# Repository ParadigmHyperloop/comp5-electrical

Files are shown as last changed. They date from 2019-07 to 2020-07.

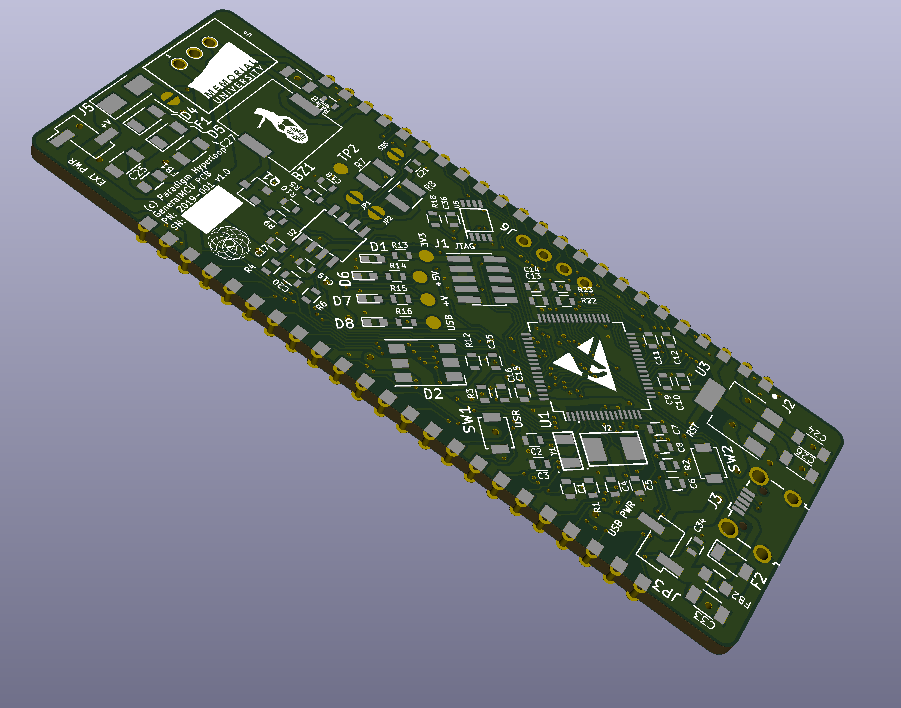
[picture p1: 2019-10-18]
GeneralMCU/pics/Capture2.3.PNG

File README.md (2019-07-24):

# comp5-electrical
All schematics and layouts in KiCad, plus some simulations https://paradigmhyperloop.com

License
See the LICENSE for full licensing details.

In summary, (you still need to read the whole thing), these boards are for Paradigm, and Paradigm only. It is shared with the world for the benefit of observers and potential Paradigm team members. If you wish to utilize these designs in any way, you must contact us first and receive written permission to utilize the designs for the purpose you require.

We don't want to be restrictive, and we will almost certainly grant you permission, but we want to know what you are using our designs for, and we want to make sure you are using them correctly and safely.

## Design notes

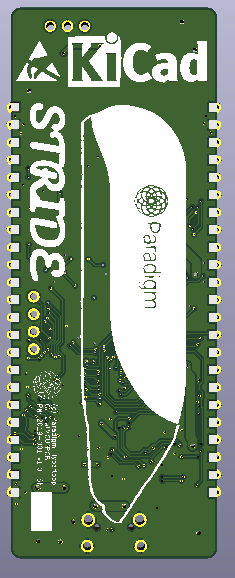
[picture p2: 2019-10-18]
GeneralMCU/pics/Capture2.2.PNG

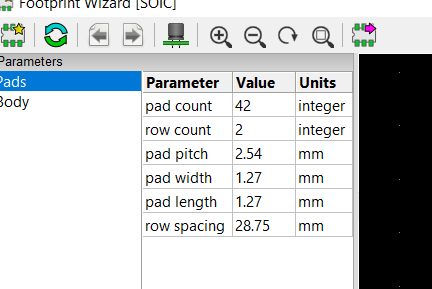
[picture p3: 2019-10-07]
GeneralMCU/pics/Footprint gen settings.PNG

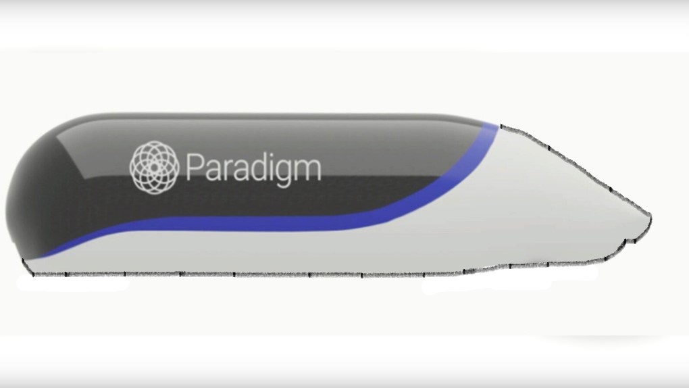
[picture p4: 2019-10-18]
GeneralMCU/pics/poddy.jpg

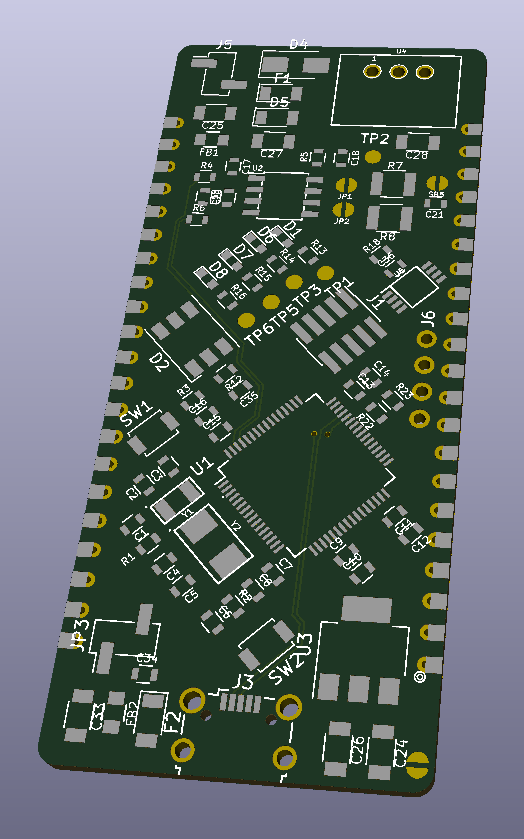
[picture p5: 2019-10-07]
GeneralMCU/docs/Capture1.PNG

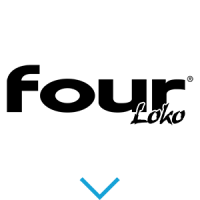
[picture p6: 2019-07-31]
meme_shield_2019/img/FLoko.png

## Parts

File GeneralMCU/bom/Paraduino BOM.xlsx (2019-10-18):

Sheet: BOM V1.0
BOM
Item # | Quantitiy | Value | References | Package | Description | Manufacturer | Manufacturer PN | Supplier | Supplier PN | Unit Cost [$CAD] | Extended [$CAD] | Notes: | Alternates
1 | 1 | Buzzer | BZ1 | Buzzer_Murata_PKMCS0909E4000-R1 | Buzzer, polarized |  |  | Digi-Key | 490-9647-1-ND |  | $0.00
2 | 10 | 0.1u | C1 C6 C7 C9 C11 C13 C15 C18 C19 C36 | SMD_pkg_0603 | Unpolarized capacitor, small symbol |  |  | Digi-Key | 1276-1005-1-ND
3 | 1 | 10n | C8 | SMD_pkg_0603 | Unpolarized capacitor, small symbol |  |  | Digi-Key | 1276-1926-1-ND
4 | 3 | 10u | C25 C27 C33 | SMD_pkg_1206 | Unpolarized capacitor, small symbol |  |  | Digi-Key | 1276-6736-1-ND
5 | 2 | 13p | C2 C3 | SMD_pkg_0603 | Unpolarized capacitor, small symbol |  |  | Digi-Key | 490-1406-1-ND
6 | 7 | 1u | C10 C12 C14 C16 C20 C34 C35 | SMD_pkg_0603 | Unpolarized capacitor, small symbol |  |  | Digi-Key | 1276-1019-1-ND
7 | 2 | 1u | C24 C26 | SMD_pkg_1206 | Unpolarized capacitor, small symbol |  |  | Digi-Key | 1276-1068-1-ND
8 | 1 | 22u | C28 | SMD_pkg_1206 | Unpolarized capacitor, small symbol |  |  | Digi-Key | 1276-6757-1-ND
9 | 1 | 4.7n | C21 | SMD_pkg_0603 | Unpolarized capacitor, small symbol |  |  | Digi-Key | 399-9091-1-ND
10 | 2 | 8p | C4 C5 | SMD_pkg_0603 | Unpolarized capacitor, small symbol |  |  | Digi-Key | 1276-1817-1-ND
11 | 1 | DNP | C17 | SMD_pkg_0603 | Unpolarized capacitor, small symbol |  |  | Digi-Key | ~
13 | 4 | 3V3 +V 5V USB | D1 | LED_0603 | Light emitting diode |  |  | Digi-Key | 732-4966-1-ND
14 | 1 | 40V 1A | D5 | D_1206 | Schottky diode, small symbol, filled shape |  |  | Digi-Key | 478-7805-1-ND
16 | 1 | D_TVS | D4 | D_SMA | Bidirectional transient-voltage-suppression diode |  |  | Digi-Key | SMAJ30ALFCT-ND | *
18 | 1 | WS2812B | D2 | LED_WS2812-PLCC6 | RGB LED with integrated controller |  |  | Digi-Key | 1568-1800-ND
19 | 1 | 32VDC 1A PTC | F1 | D_1206 | Fuse, small symbol |  |  | Digi-Key | 507-1801-1-ND
20 | 1 | 500mA 5V PTC | F2 | D_1206 | Fuse, small symbol |  |  | Digi-Key | 507-1813-1-ND
21 | 2 | FB | FB1 FB2 | SMD_pkg_0805 | Ferrite bead, small symbol |  |  | Digi-Key | 732-1620-1-ND
22 | 1 | ARM_JTAG_SWD | J1 | PinHeader_2x05_P1.27mm_Vertical_SMD | Cortex Debug Connector, standard ARM Cortex-M SWD and JTAG interface |  |  | Digi-Key | 609-6529-ND | http://infocenter.arm.com/help/topic/com.arm.doc.faqs/attached/13634/cortex_debug_connectors.pdf
23 | 1 | OLED | J6 | I2C_OLED | Generic connector, single row, 01x04, script generated (kicad-library-utils/schlib/autogen/connector/) |  |  | Digi-Key | S7002-ND
24 | 1 | USB_B_Micro | J3 | USB_Micro-B_Wuerth-629105150521_CircularHoles | USB Micro Type B connector |  |  | Digi-Key | 609-4616-1-ND
25 | 3 | Jumper_NC_Small | JP1 JP2 JP3 J5 | Pin_Header_Straight_1x02_Pitch2.54mm_SMD_Pin1Left | Jumper, normally closed, small symbol |  |  | Digi-Key | 952-1913-ND
26 | 3 | Jumper_NC_Small | JP1 JP2 JP3 | Pin Jumper |  |  |  | Digi-Key | S9337-ND
27 | 1 | Q_NMOS_DGS | Q1 | SOT-23 | N-MOSFET transistor, gate/source/drain |  |  | Digi-Key | ZXM61N03FCT-ND
28 | 5 | 0 | R4 R6 R11 R20 R21 | SMD_pkg_0603 | Resistor, small US symbol |  |  | Digi-Key | 311-0.0GRCT-ND
29 | 8 | 10k | R1 R2 R3 R12 R13 R14 R15 R16 | SMD_pkg_0603 | Resistor, small US symbol |  |  | Digi-Key | RNCP0603FTD10K0CT-ND
30 | 2 | 1k | R9 R10 | SMD_pkg_0603 | Resistor, small US symbol |  |  | Digi-Key | RNCP0603FTD1K00CT-ND
31 | 3 | 4.7k | R18 R22 R23 | SMD_pkg_0603 | Resistor, small US symbol |  |  | Digi-Key | MCT0603-4.70K-CFCT-ND
32 | 2 | 60 | R7 R8 | SMD_pkg_1210 | Resistor, small US symbol |  |  | Digi-Key | 541-0.0VCT-ND
33 | 1 | DNP | R5 | SMD_pkg_0603 | Resistor, small US symbol |  |  | Digi-Key | ~
34 | 2 | RESET, USER | SW1 SW2 | SW_SPST_B3U-1000P | Push button switch, generic, two pins |  |  | Digi-Key | SW1020CT-ND
36 | 1 | AZ1117-3.3 | U3 | SOT-223-3_TabPin2 | 1A 20V Fixed LDO Linear Regulator, 1.2V, SOT-89/SOT-223/TO-220/TO-252/TO-263 |  |  | Digi-Key | AZ1117EH-3.3TRG1DICT-ND
37 | 1 | DS18B20 | U5 | MSOP-8 | Programmable Resolution 1-Wire Digital Thermometer MSOP-8 |  |  | Digi-Key | DS18B20U+T&RCT-ND | http://datasheets.maximintegrated.com/en/ds/DS18B20.pdf
38 | 1 | P78E05-1000 | U4 | Recom_INNOLINE-R-78E |  |  |  | Digi-Key | 102-5018-ND
39 | 1 | SN65HVD230 | U2 | SOIC-8_N | CAN Bus Transceivers, 3.3V, 1Mbps, Low-Power capabilities, SOIC |  |  | Digi-Key | 296-11654-1-ND | http://www.ti.com/lit/ds/symlink/sn65hvd230.pdf
40 | 1 | STM32F303R6Tx | U1 | LQFP-64_10x10mm_Pitch0.5mm | ARM Cortex-M4 MCU, 32KB flash, 12KB RAM, 72MHz, 2-3.6V, 51 GPIO, LQFP-64 |  |  | Digi-Key | 497-15163-ND | http://www.st.com/st-web-ui/static/active/en/resource/technical/document/datasheet/DM00092070.pdf
41 | 1 | 32.768kHz | Y1 | Crystal_NDK_NX3215SA | Two pin crystal, small symbol |  |  | Digi-Key | 644-1159-1-ND
42 | 1 | 8MHz | Y2 | Crystal_L5_W3.2 | Two pin crystal, small symbol |  |  | Digi-Key | 887-1667-1-ND
43 | 2 |  | J2 | 23 pin tht conn |  |  |  |  | S1012EC-23-ND
 |  |  |  |  |  |  |  |  |  | 1528-2009-ND
 |  |  |  |  |  |  |  | ~ | $49.44

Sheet: Import
Component | Description | Part | References | Value | Footprint | Quantity Per PCB | Datasheet | Datasheet2
1 | Buzzer, polarized | Buzzer | BZ1 | Buzzer | Buzzer_Murata_PKMCS0909E4000-R1 | 1 | 490-9647-1-ND
2 | Unpolarized capacitor, small symbol | C_Small | C1 C6 C7 C9 C11 C13 C15 C18 C19 C36 | 0.1u | SMD_pkg_0603 | 10 | ~
3 | Unpolarized capacitor, small symbol | C_Small | C22 C23 | 0.1u |  | 2 | ~
4 | Unpolarized capacitor, small symbol | C_Small | C8 | 10n | SMD_pkg_0603 | 1 | ~
5 | Unpolarized capacitor, small symbol | C_Small | C25 C27 C33 | 10u | SMD_pkg_1206 | 3 | ~
6 | Unpolarized capacitor, small symbol | C_Small | C2 C3 | 13p | SMD_pkg_0603 | 2 | ~
7 | Unpolarized capacitor, small symbol | C_Small | C10 C12 C14 C16 C20 C34 C35 | 1u | SMD_pkg_0603 | 7 | ~
8 | Unpolarized capacitor, small symbol | C_Small | C24 C26 | 1u | SMD_pkg_1206 | 2 | ~
9 | Unpolarized capacitor, small symbol | C_Small | C28 | 22u | SMD_pkg_1206 | 1 | ~
10 | Unpolarized capacitor, small symbol | C_Small | C21 | 4.7n | SMD_pkg_0603 | 1 | ~
11 | Unpolarized capacitor, small symbol | C_Small | C4 C5 | 8p | SMD_pkg_0603 | 2 | ~
12 | Unpolarized capacitor, small symbol | C_Small | C17 | DNP | SMD_pkg_0603 | 1 | ~
13 | Light emitting diode | LED | D7 | +V | LED_0603 | 1 | ~
14 | Light emitting diode | LED | D1 | 3V3 | LED_0603 | 1 | 732-4966-1-ND
15 | Schottky diode, small symbol, filled shape | D_Schottky_Small_ALT | D5 | 40V 1A | D_1206 | 1 | 478-7805-1-ND
16 | Light emitting diode | LED | D6 | 5V | LED_0603 | 1 | ~
17 | Bidirectional transient-voltage-suppression diode | D_TVS | D4 | D_TVS | D_SMA | 1 | ~
18 | Bidirectional dual transient-voltage-suppression diode, center on pin 3 | D_TVS_x2_AAC | D3 | NUP2105L |  | 1 | ~
19 | Light emitting diode | LED | D8 | USB | LED_0603 | 1 | ~
20 | RGB LED with integrated controller | WS2812 | D2 | WS2812B | LED_WS2812-PLCC6 | 1 | 1568-1800-ND
21 | Fuse, small symbol | Fuse_Small | F1 | 32VDC 1A PTC | D_1206 | 1 | ~
22 | Fuse, small symbol | Fuse_Small | F2 | 500mA PTC | D_1206 | 1 | ~
23 | Ferrite bead, small symbol | Ferrite_Bead_Small | FB1 FB2 | FB | SMD_pkg_0805 | 2 | 732-1620-1-ND
24 | Cortex Debug Connector, standard ARM Cortex-M SWD and JTAG interface | Conn_ARM_JTAG_SWD_10 | J1 | ARM_JTAG_SWD | PinHeader_2x05_P1.27mm_Vertical_SMD | 1 | http://infocenter.arm.com/help/topic/com.arm.doc.faqs/attached/13634/cortex_debug_connectors.pdf
25 | Generic connector, single row, 01x04, script generated (kicad-library-utils/schlib/autogen/connector/) | Conn_01x04 | J4 | Conn_01x04 |  | 1 | ~
26 | Generic connector, single row, 01x04, script generated (kicad-library-utils/schlib/autogen/connector/) | Conn_01x04 | J6 | OLED | I2C_OLED | 1 | ~
27 | Generic connector, single row, 01x02, script generated (kicad-library-utils/schlib/autogen/connector/) | Conn_01x02 | J5 | PWR | Pin_Header_Straight_1x02_Pitch2.54mm_SMD_Pin1Left | 1 | ~
28 | Generic connector, double row, 02x21, counter clockwise pin numbering scheme (similar to DIP packge numbering), script generated (kicad-library-utils/schlib/autogen/connector/) | Conn_02x21_Counter_Clockwise | J2 | SMD castellation PKG |  | 1 | ~
29 | USB Micro Type B connector | USB_B_Micro | J3 | USB_B_Micro | USB_Micro-B_Wuerth-629105150521_CircularHoles | 1 | ~
30 | Jumper, normally closed, small symbol | Jumper_NC_Small | JP1 JP2 SB5 SB6 | Jumper_NC_Small | JUMPER_EGG | 4 | ~
31 | Jumper, normally closed, small symbol | Jumper_NC_Small | JP3 | Jumper_NC_Small | Pin_Header_Straight_1x02_Pitch2.54mm_SMD_Pin1Left | 1 | ~
32 | N-MOSFET transistor, gate/source/drain | Q_NMOS_GSD | Q1 | Q_NMOS_DGS | SOT-23 | 1 | ~
33 | Resistor, small US symbol | R_Small_US | R4 R6 R11 R20 R21 | 0 | SMD_pkg_0603 | 5 | ~
34 | Resistor, small US symbol | R_Small_US | R1 R2 R3 R12 R13 R14 R15 R16 | 10k | SMD_pkg_0603 | 8 | ~
35 | Resistor, small US symbol | R_Small_US | R9 R10 | 1k | SMD_pkg_0603 | 2 | ~
36 | Resistor, small US symbol | R_Small_US | R18 R22 R23 | 4.7k | SMD_pkg_0603 | 3 | ~
37 | Resistor, small US symbol | R_Small_US | R7 R8 | 60 | SMD_pkg_1210 | 2 | ~
38 | Resistor, small US symbol | R_Small_US | R5 | DNP | SMD_pkg_0603 | 1 | ~
39 | Jumper, normally closed, small symbol | Jumper_NC_Small | SB1 SB2 SB3 SB4 | Jumper_NC_Small |  | 4 | ~
40 | Push button switch, generic, two pins | SW_Push | SW2 | RESET | SW_SPST_B3U-1000P | 1 | SW1020CT-ND
41 | Push button switch, generic, two pins | SW_Push | SW1 | USER | SW_SPST_B3U-1000P | 1 | SW1020CT-ND
42 | 1A 20V Fixed LDO Linear Regulator, 1.2V, SOT-89/SOT-223/TO-220/TO-252/TO-263 | AZ1117-3.3 | U3 | AZ1117-3.3 | SOT-223-3_TabPin2 | 1 | AZ1117EH-3.3TRG1DICT-ND
43 | Programmable Resolution 1-Wire Digital Thermometer MSOP-8 | DS18B20U | U5 | DS18B20 | MSOP-8 | 1 | http://datasheets.maximintegrated.com/en/ds/DS18B20.pdf
44 |  | V_REG | U4 | P78E05-1000 | Recom_INNOLINE-R-78E | 1 | 102-5018-ND
45 | CAN Bus Transceivers, 3.3V, 1Mbps, Low-Power capabilities, SOIC | SN65HVD230 | U2 | SN65HVD230 | SOIC-8_N | 1 | http://www.ti.com/lit/ds/symlink/sn65hvd230.pdf
46 | ARM Cortex-M4 MCU, 32KB flash, 12KB RAM, 72MHz, 2-3.6V, 51 GPIO, LQFP-64 | STM32F303R6Tx | U1 | STM32F303R6Tx | LQFP-64_10x10mm_Pitch0.5mm | 1 | 497-15163-ND | http://www.st.com/st-web-ui/static/active/en/resource/technical/document/datasheet/DM00092070.pdf
47 | Two pin crystal, small symbol | Crystal_Small | Y1 | 32.768kHz | Crystal_NDK_NX3215SA | 1 | 644-1159-1-ND
48 | Two pin crystal, small symbol | Crystal_Small | Y2 | 8MHz | Crystal_L5_W3.2 | 1 | 887-1667-1-ND
Component Groups: | 48
Component Count: | 91
Fitted Components: | 91
Number of PCBs: | 1
Total components: | 91
Schematic Version: | v1.0
Schematic Date: | 2019-08-13
BoM Date: | 2019-09-16 18:52
Schematic Source: | C:\projects\hyperloop\comp5-electrical\GeneralMCU\GeneralMCU.sch
KiCad Version: | Eeschema (5.0.2)-1

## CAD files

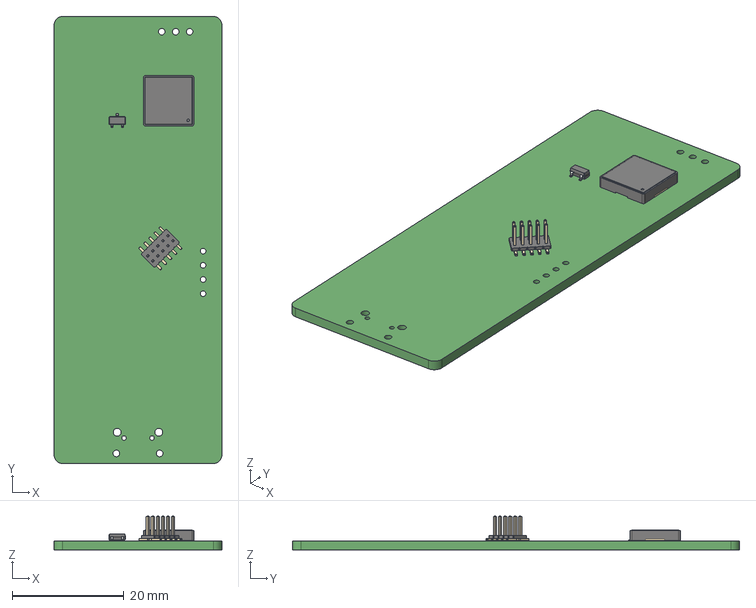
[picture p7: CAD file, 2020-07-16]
BigSur/Models/GeneralMCU.step
30.0 x 80.0 x 6.05 mm

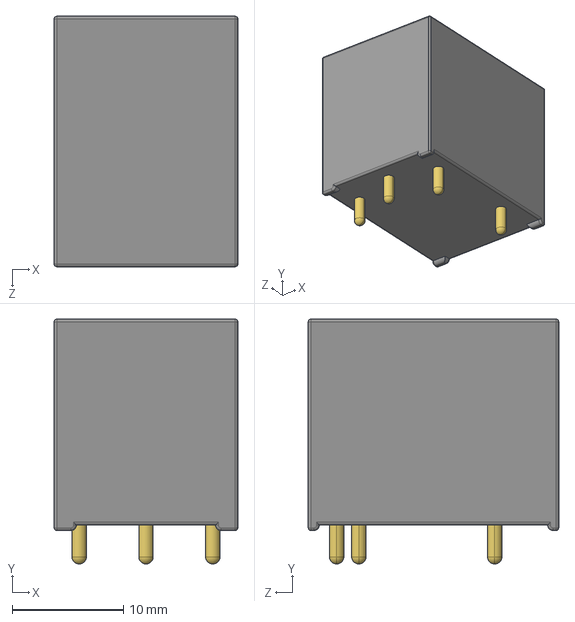
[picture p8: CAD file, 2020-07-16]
BigSur/Models/G5LE-1A-VDDC12.STEP
16.5 x 22.0 x 22.5 mm
Relay_Body
Relay_Contacts

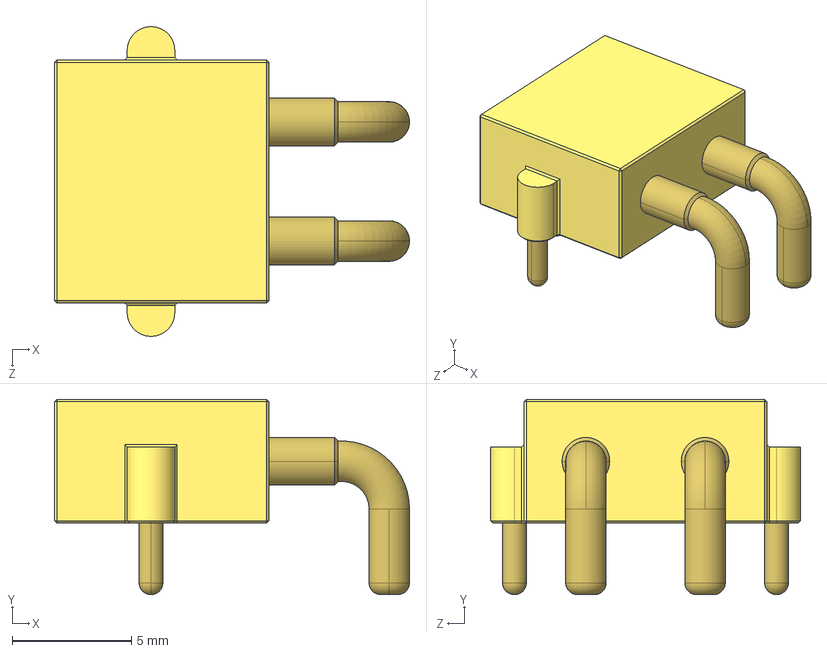
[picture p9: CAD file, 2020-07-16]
BigSur/Models/XT30.STEP
14.9 x 8.20 x 13.0 mm
XT30_Plastic
XT30_Contacts

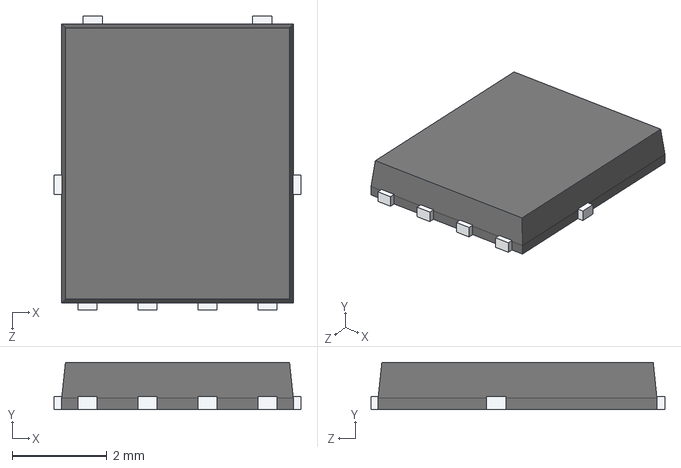
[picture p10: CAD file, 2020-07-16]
BigSur/Models/NTS12120EMFS-D.STEP
5.22 x 1.00 x 6.22 mm
NTS12120EMFS-D_Body
NTS12120EMFS-D_Contacts

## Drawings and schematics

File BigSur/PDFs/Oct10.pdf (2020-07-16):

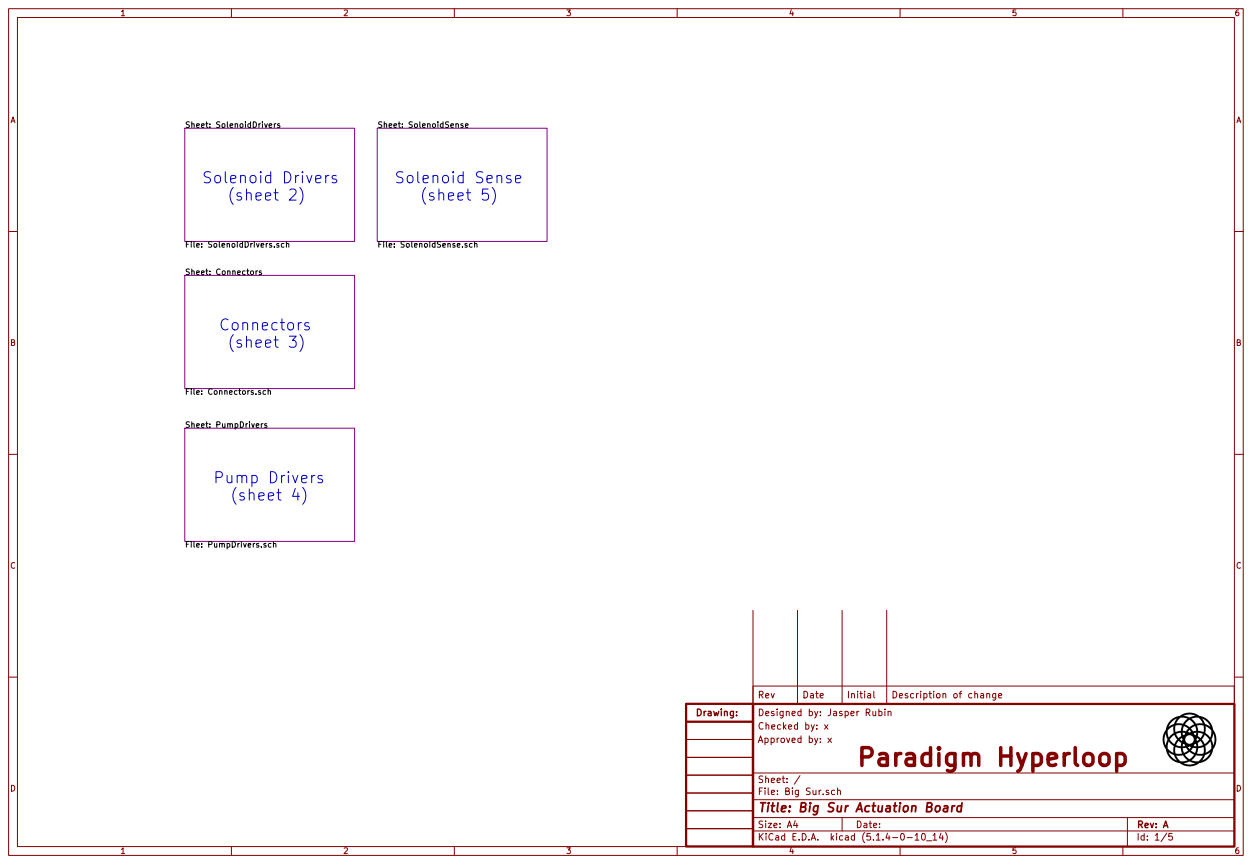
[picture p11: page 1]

Sheet: SolenoidDrivers File: SolenoidDrivers.sch Sheet: Connectors File: Connectors.sch Sheet: PumpDrivers

Sheet: SolenoidSense File: SolenoidSense.sch Connectors

Id: 1/5 Title: Big Sur Actuation Board

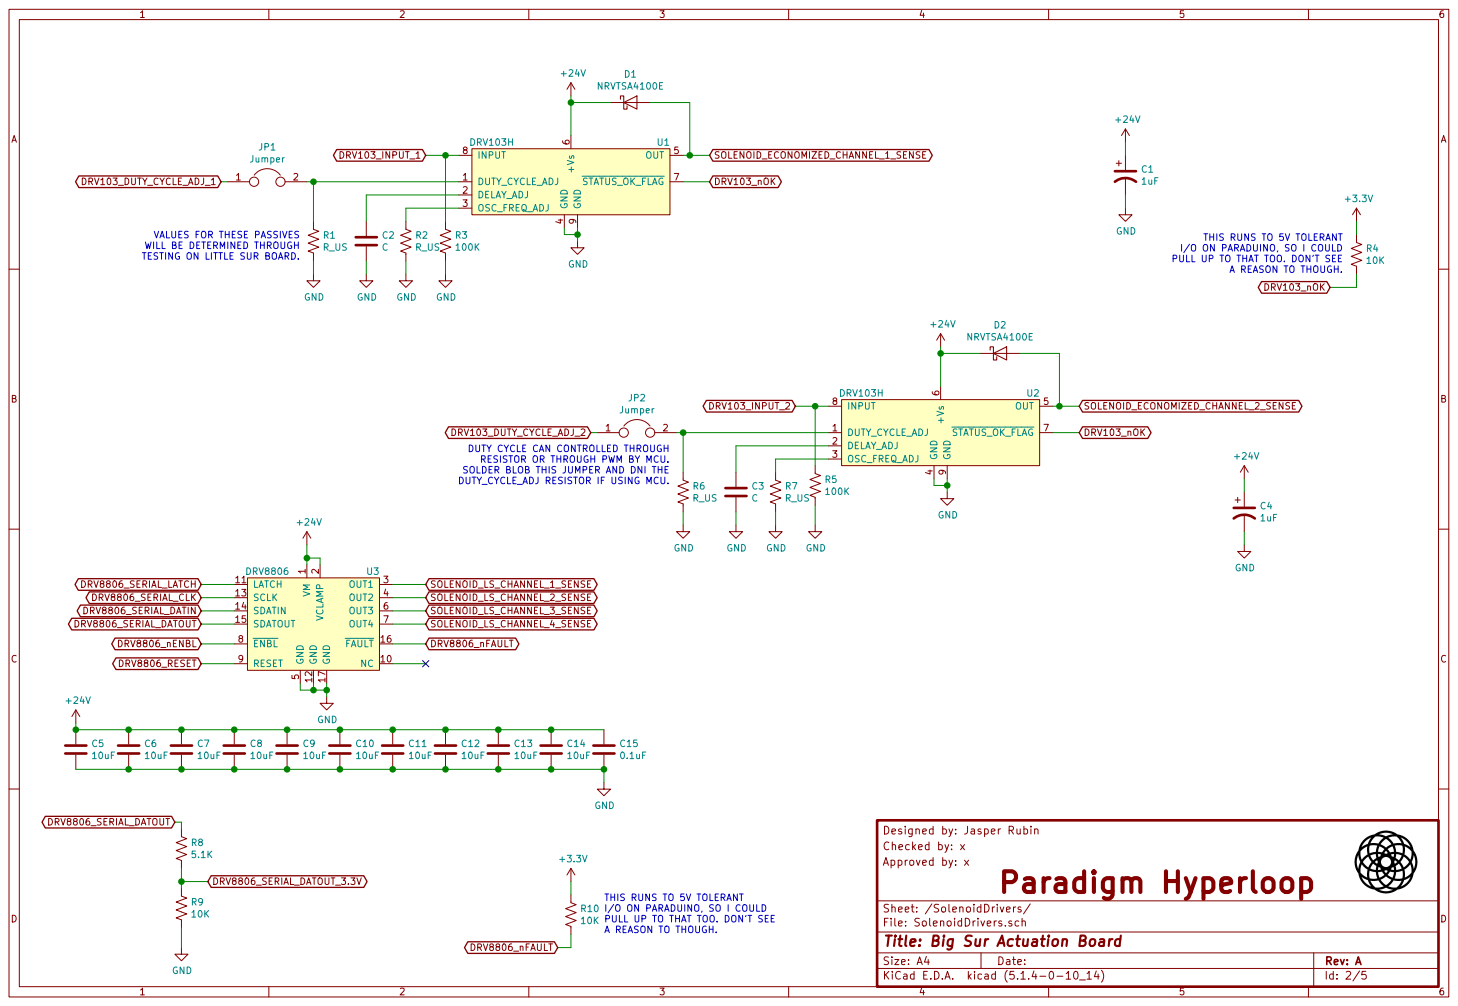
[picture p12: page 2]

VALUES FOR THESE PASSIVES WILL BE DETERMINED THROUGH

I/O ON PARADUINO, SO I COULD
PULL UP TO THAT TOO. DONT SEE

DUTY CYCLE CAN CONTROLLED THROUGH
RESISTOR OR THROUGH PWM BY MCU. SOLDER BLOB THIS JUMPER AND DNI THE DUTY_CYCLE_ADJ RESISTOR IF USING MCU.

Checked by: x
Approved by: x
File: SolenoidDrivers.sch Sheet: /SolenoidDrivers/Paradigm Hyperloop

THIS RUNS TO 5V TOLERANT
A REASON TO THOUGH.

Id: 2/5 Title: Big Sur Actuation Board

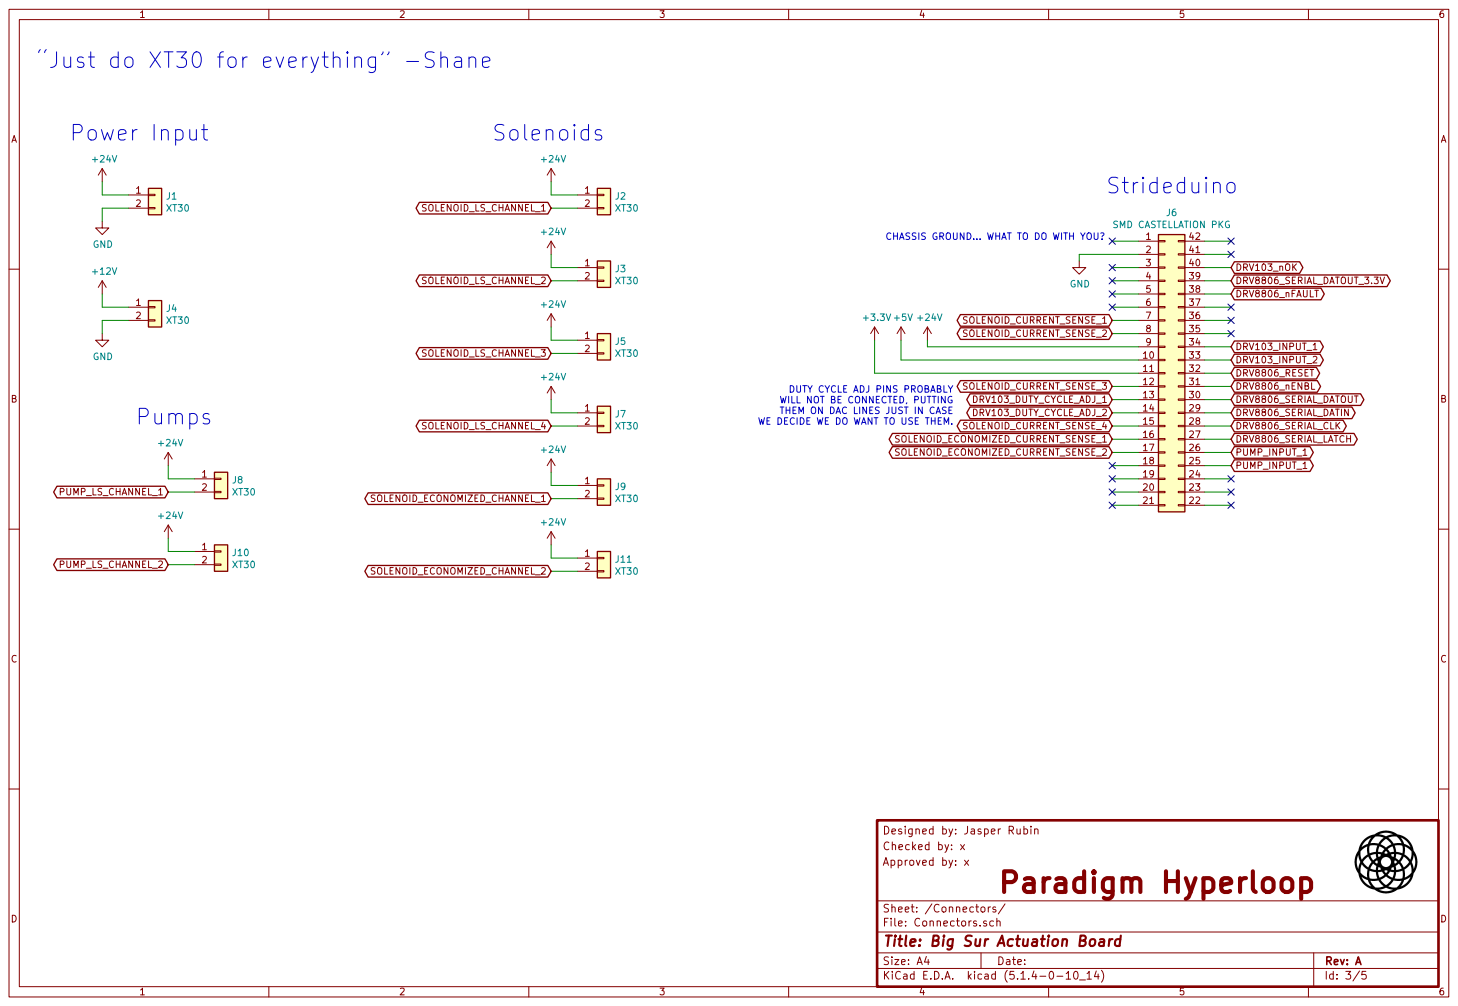
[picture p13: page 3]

CHASSIS GROUND WHAT TO DO WITH YOU? Power Input
+24V GND

DUTY CYCLE ADJ PINS PROBABLY WILL NOT BE CONNECTED, PUTTING

Designed by: Jasper Rubin
Checked by: x
Approved by: x

Id: 3/5 Title: Big Sur Actuation Board

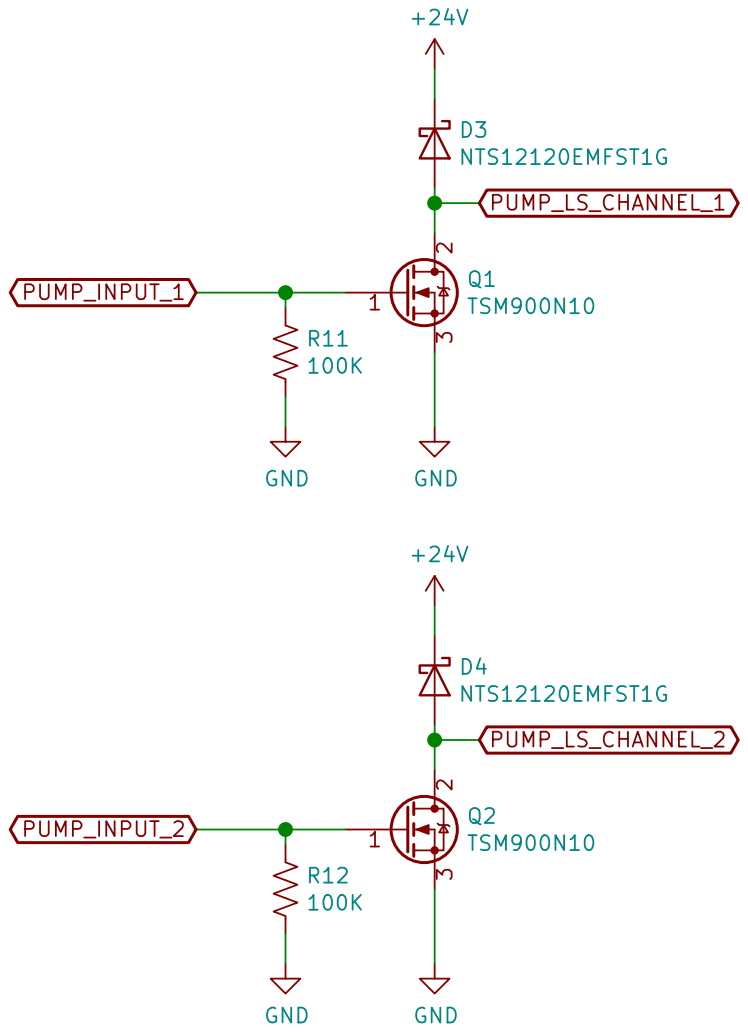
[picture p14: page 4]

Designed by: Jasper Rubin
Checked by:
Approved by:

Sheet: /PumpDrivers/
File: PumpDrivers.sch
Id: 4/5 Title: Big Sur Actuation Board

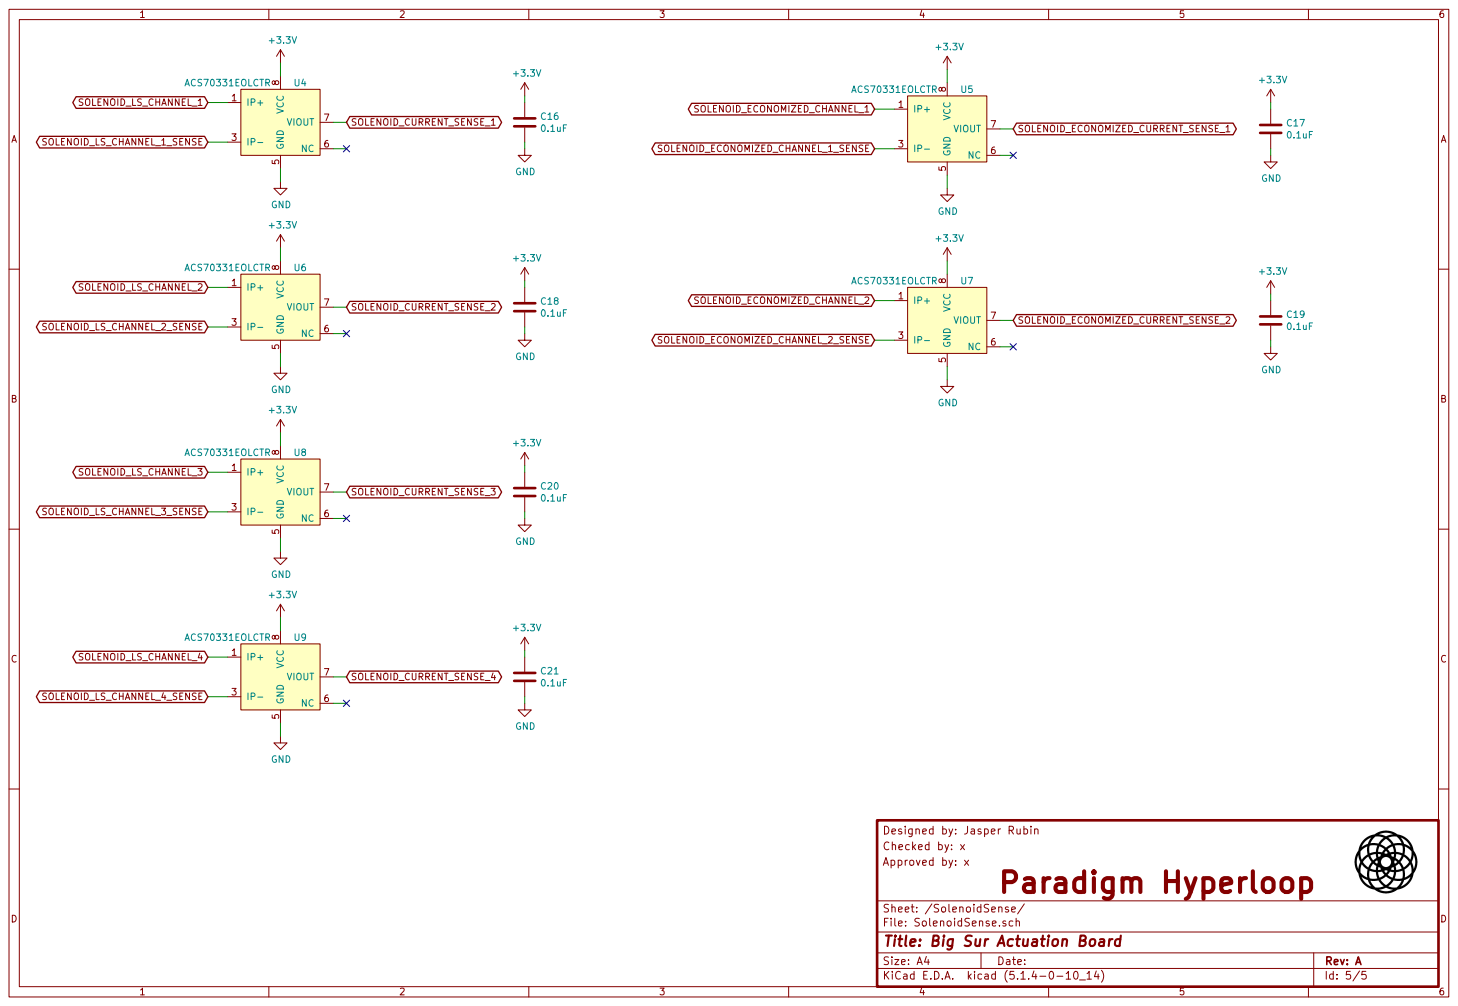
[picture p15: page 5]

Designed by: Jasper Rubin
Checked by: x
Approved by: x
File: SolenoidSense.sch Sheet: /SolenoidSense/Paradigm Hyperloop

Id: 5/5 Title: Big Sur Actuation Board

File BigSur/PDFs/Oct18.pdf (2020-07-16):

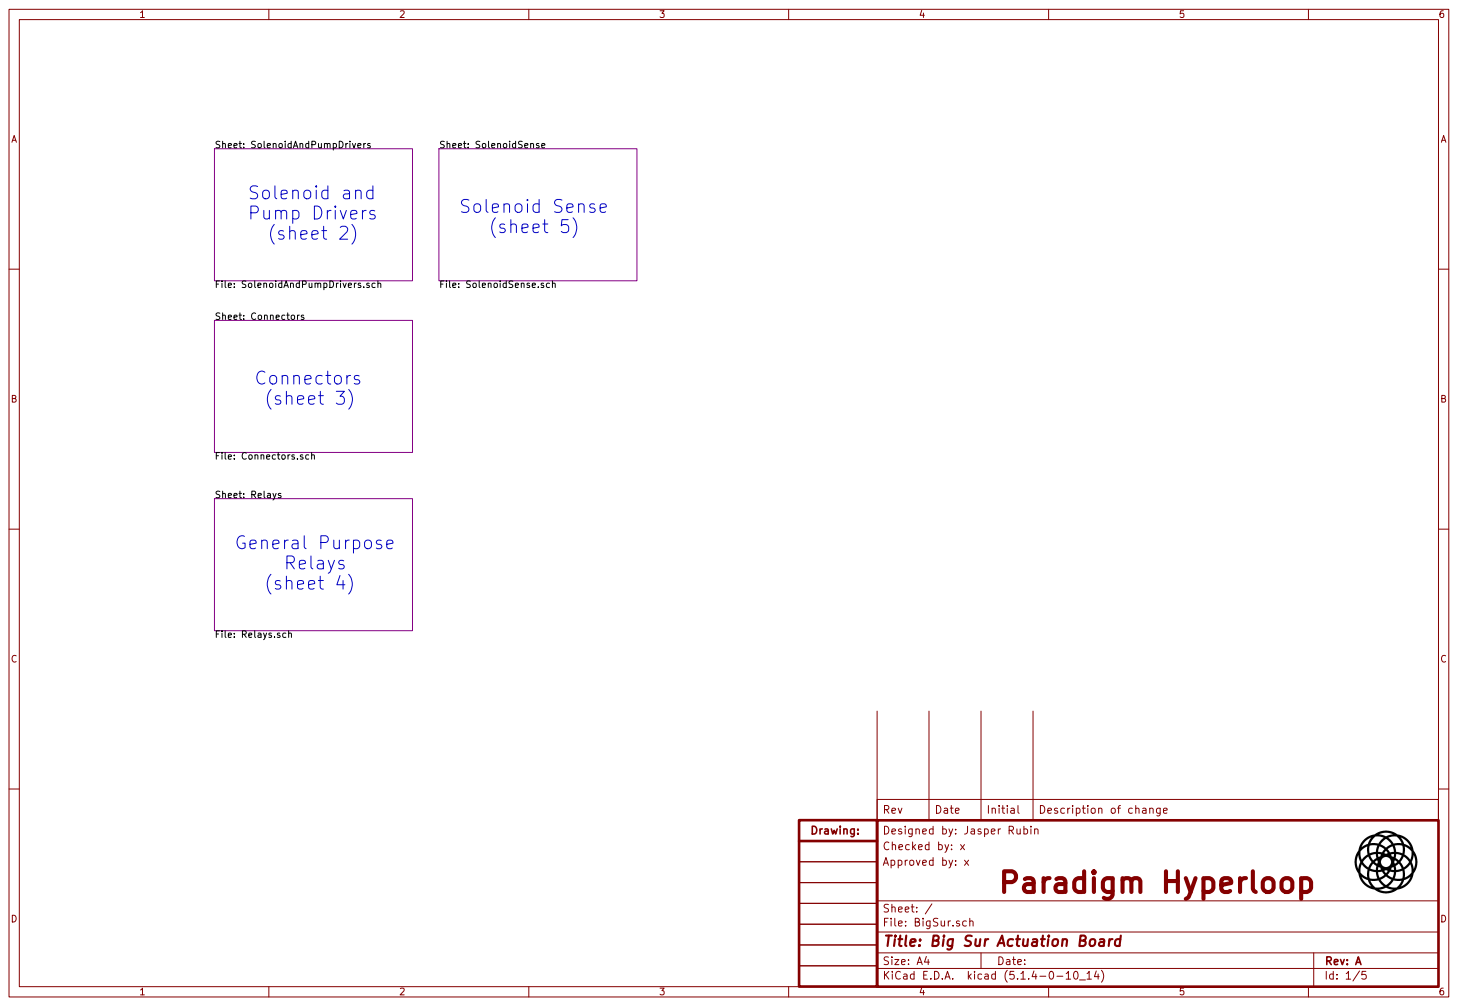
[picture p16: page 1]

Sheet: SolenoidSense File: SolenoidSense.sch Connectors

File: SolenoidAndPumpDrivers.sch Sheet: Connectors File: Connectors.sch Sheet: Relays

Id: 1/5 Title: Big Sur Actuation Board

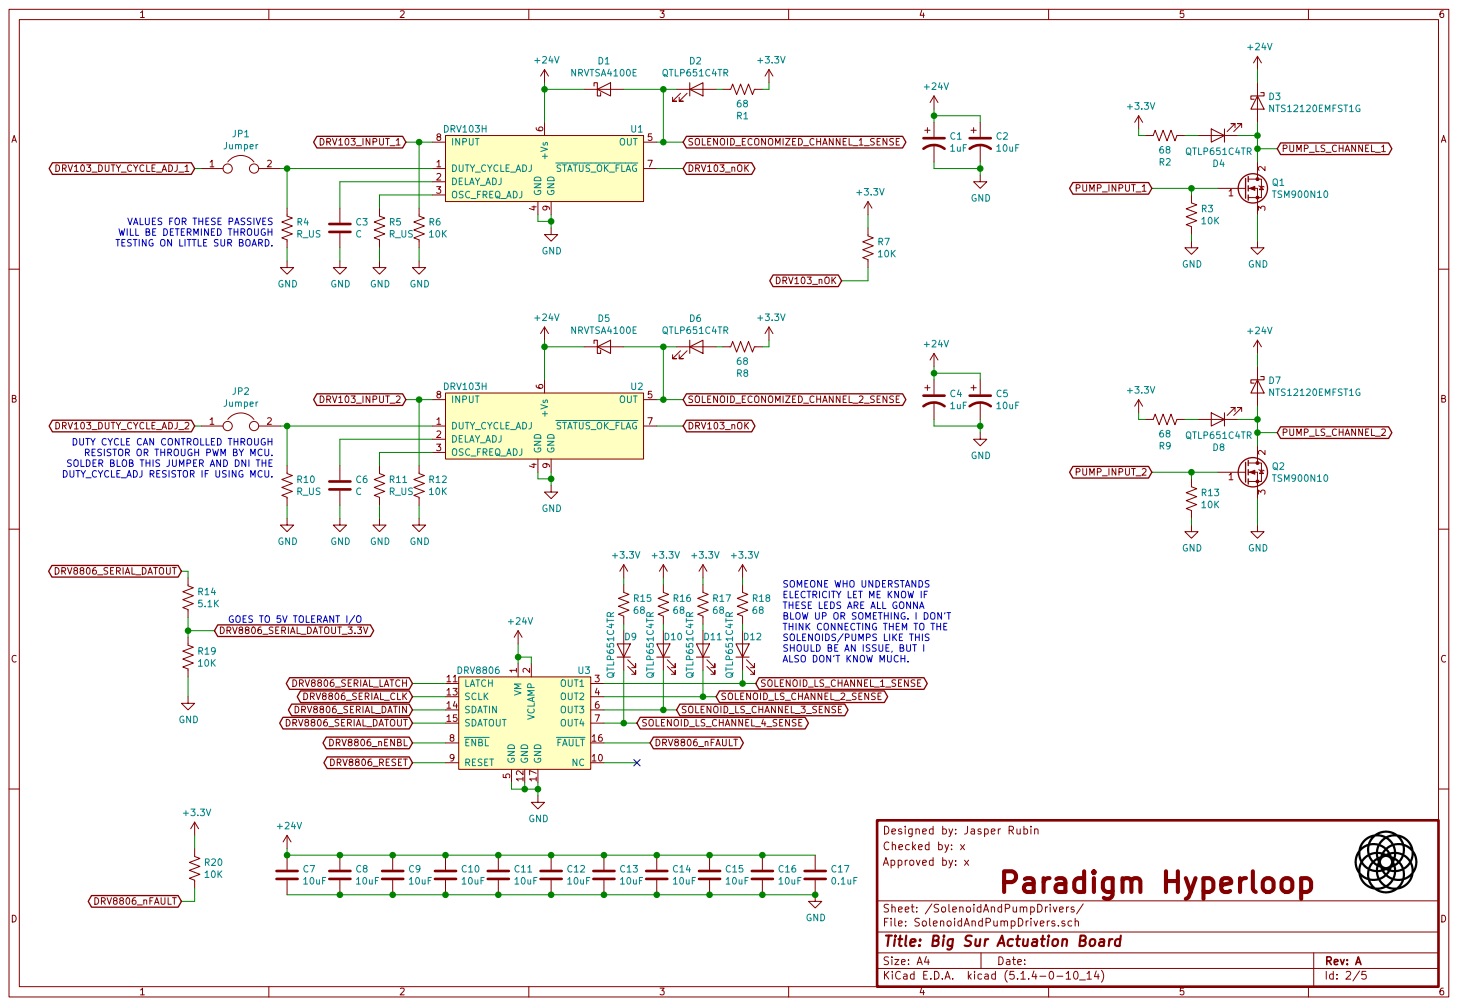
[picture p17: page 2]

VALUES FOR THESE PASSIVES WILL BE DETERMINED THROUGH

TESTING ON LITTLE SUR BOARD. DUTY CYCLE CAN CONTROLLED THROUGH

RESISTOR OR THROUGH PWM BY MCU. SOLDER BLOB THIS JUMPER AND DNI THE DUTY_CYCLE_ADJ RESISTOR IF USING MCU. GOES TO 5V TOLERANT I/O

SOMEONE WHO UNDERSTANDS
ELECTRICITY LET ME KNOW IF
Designed by: Jasper Rubin R18
THESE LEDS ARE ALL GONNA
BLOW UP OR SOMETHING. I DONT
THINK CONNECTING THEM TO THE
SOLENOIDS/PUMPS LIKE THIS
SHOULD BE AN ISSUE, BUT I ALSO DONT KNOW MUCH.

Sheet: /SolenoidAndPumpDrivers/
File: SolenoidAndPumpDrivers.sch
Id: 2/5 Title: Big Sur Actuation Board

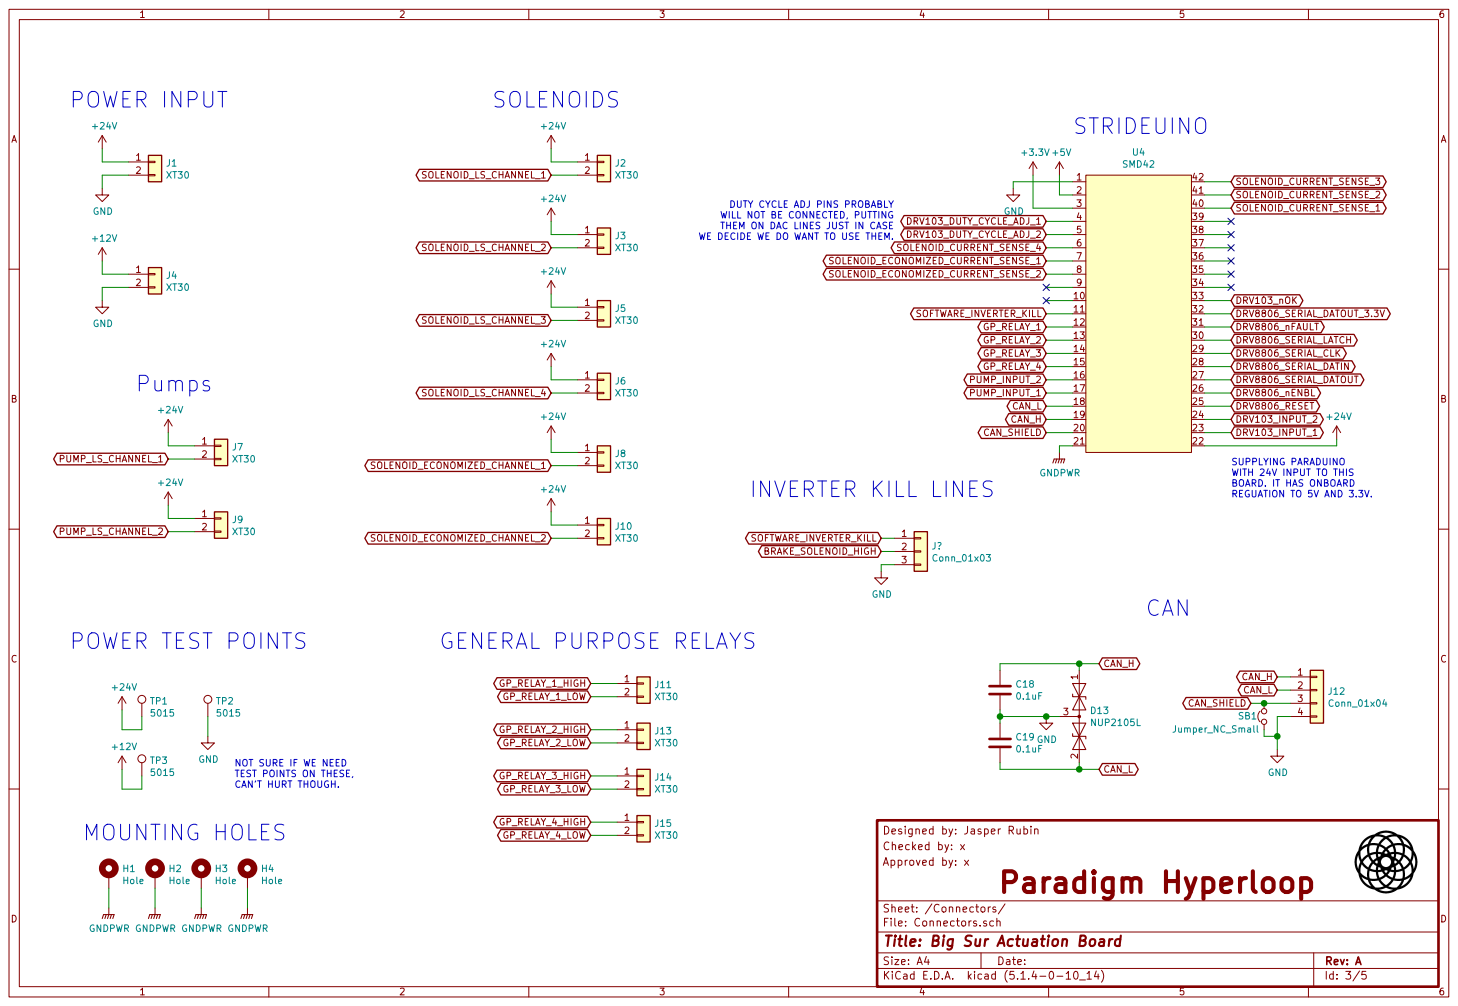
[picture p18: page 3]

THEM ON DAC LINES JUST IN CASE WE DECIDE WE DO WANT TO USE THEM. Pumps

SUPPLYING PARADUINO WITH 24V INPUT TO THIS

NOT SURE IF WE NEED

Designed by: Jasper Rubin
Checked by: x
Approved by: x

Id: 3/5 Title: Big Sur Actuation Board

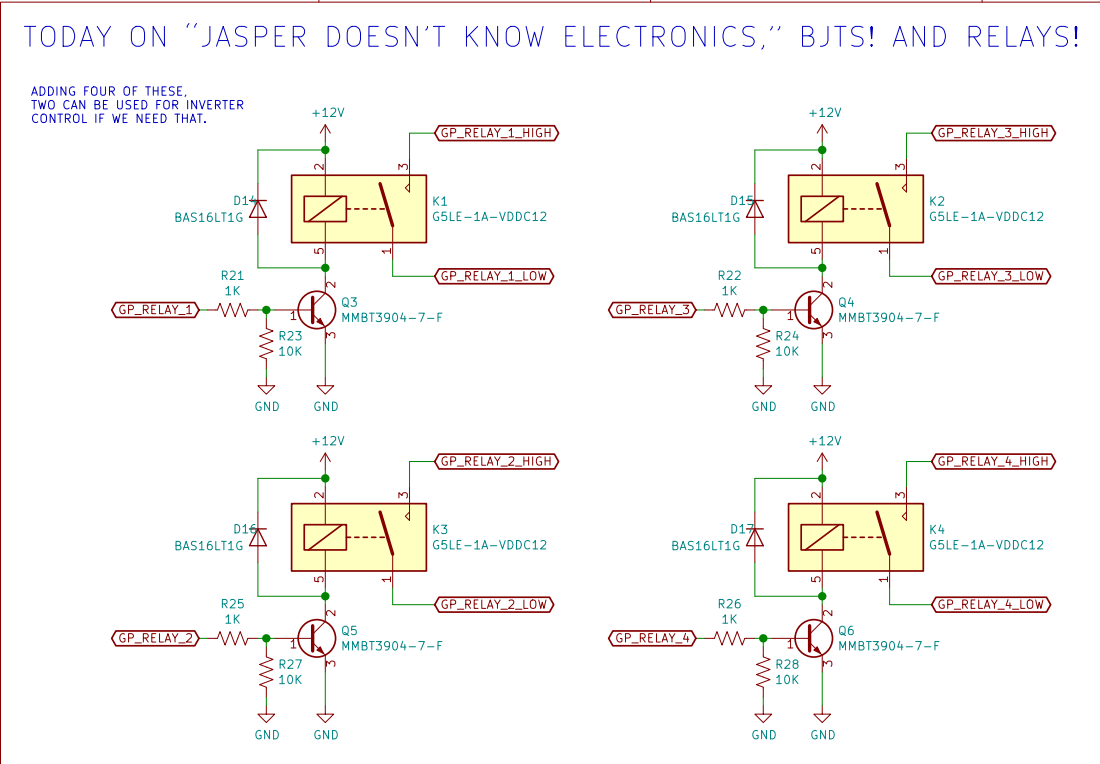
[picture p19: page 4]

GP_RELAY_3 TODAY ON JASPER DOESNT KNOW ELECTRONICS, BJTS! AND RELAYS! ADDING FOUR OF THESE, TWO CAN BE USED FOR INVERTER

CONTROL IF WE NEED THAT.

Designed by: Jasper Rubin
Checked by: x
Approved by: x

Sheet: /Relays/
File: Relays.sch
Id: 4/5 Title: Big Sur Actuation Board

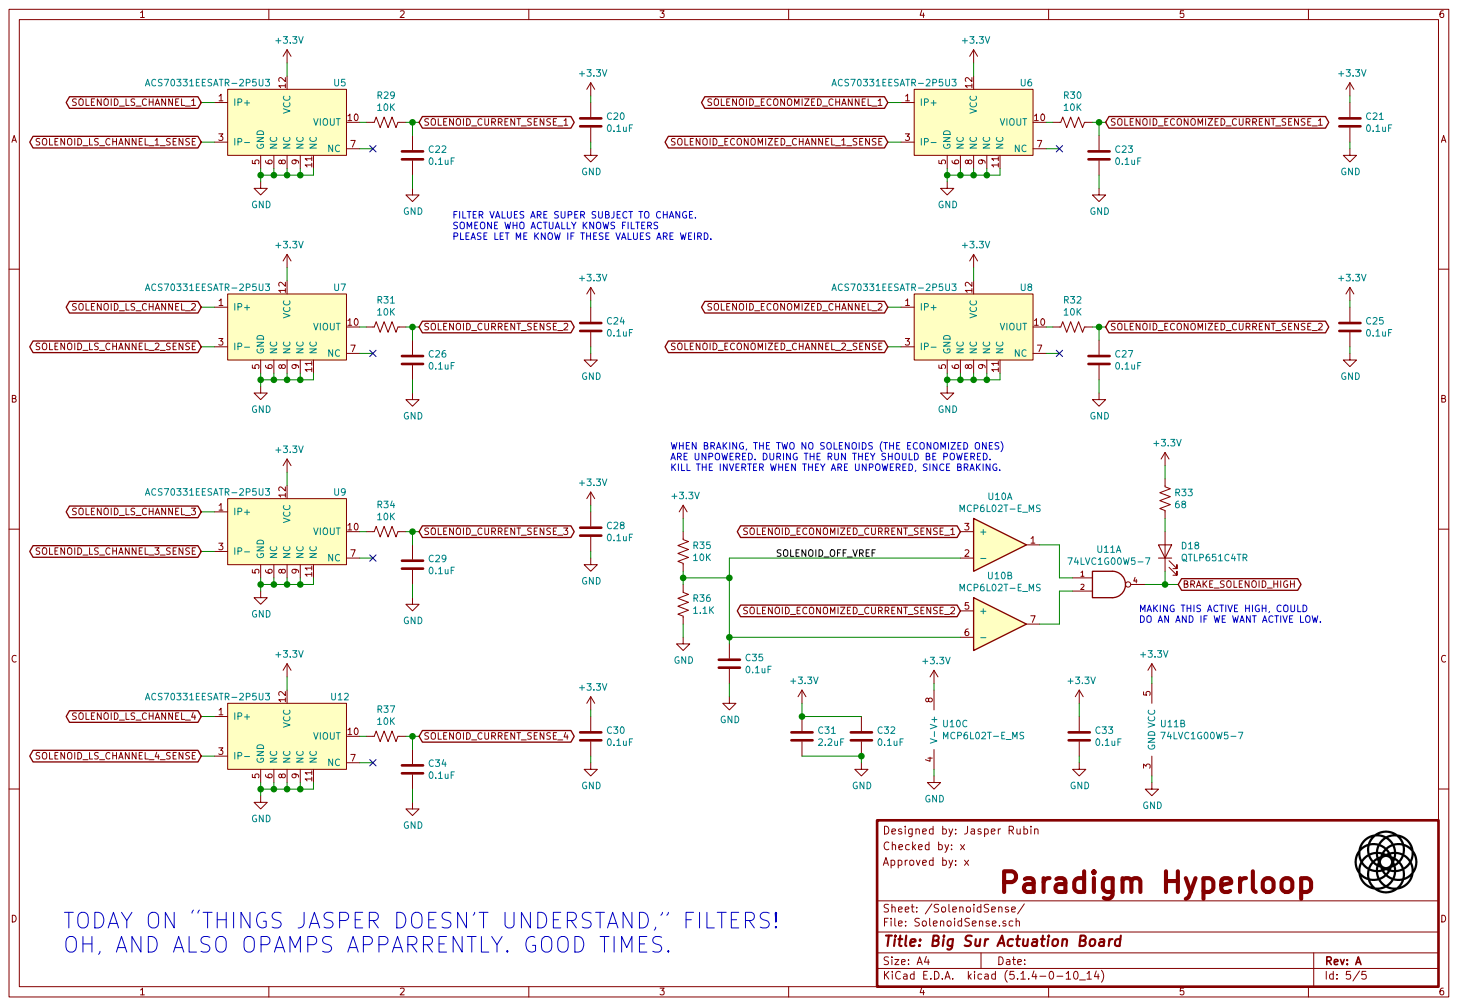
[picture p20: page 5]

FILTER VALUES ARE SUPER SUBJECT TO CHANGE. SOMEONE WHO ACTUALLY KNOWS FILTERS

PLEASE LET ME KNOW IF THESE VALUES ARE WEIRD. WHEN BRAKING, THE TWO NO SOLENOIDS (THE ECONOMIZED ONES) ARE UNPOWERED. DURING THE RUN THEY SHOULD BE POWERED. KILL THE INVERTER WHEN THEY ARE UNPOWERED, SINCE BRAKING.

DO AN AND IF WE WANT ACTIVE LOW. TODAY ON THINGS JASPER DOESNT UNDERSTAND, FILTERS!

Designed by: Jasper Rubin
Checked by: x
Approved by: x
File: SolenoidSense.sch Sheet: /SolenoidSense/Paradigm Hyperloop

OH, AND ALSO OPAMPS APPARRENTLY. GOOD TIMES.

Id: 5/5 Title: Big Sur Actuation Board

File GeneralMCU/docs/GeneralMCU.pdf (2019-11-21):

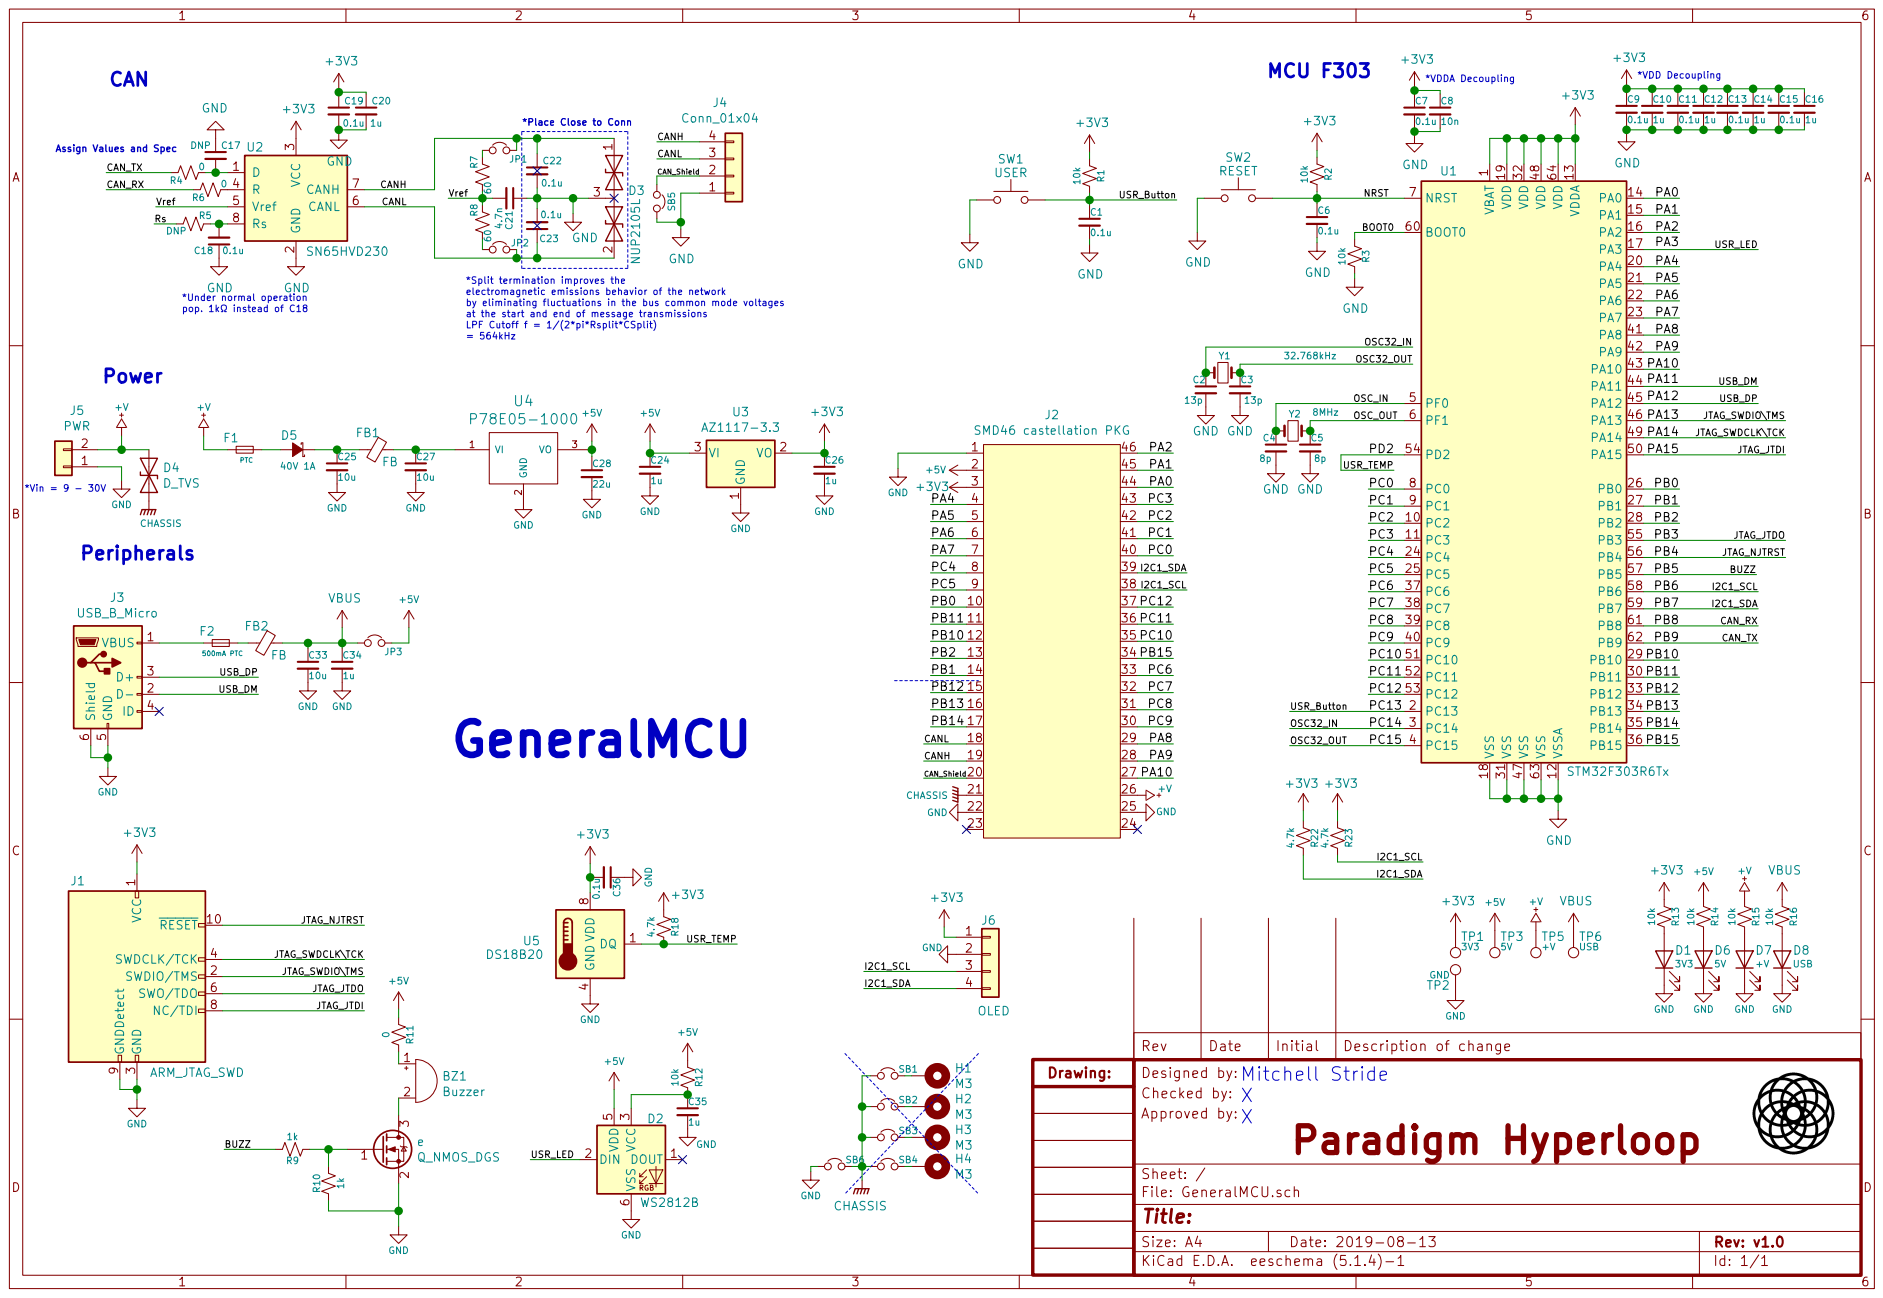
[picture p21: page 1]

*Place Close to Conn Power

*Place Close to Conn

1 PC2 10 PC3 11 VSSA 12 VDDA 13 PA0 14 PA1 15 PA2 16 PA3 17 VSS 18 VDD 19 PC13 2 PA4 20 PA5 21 PA6 22 PA7 23 PC4 24 PC5 25 PB0 26 PB1 27 PB2 28 PB10 29 PC14 3 PB11 30 VSS 31 VDD 32 PB12 33 PB13 34 PB14 35 PB15 36 PC6 37 PC7 38 PC8 39 PC15 4 PC9 40 PA8 41 PA9 42 PA10 43 PA11 44 PA12 45 PA13 46 VSS 47 VDD 48 PA14 49 PF0 5 PA15 50 PC10 51 PC11 52 PC12 53 PD2 54 PB3 55 PB4 56 PB5 57 PB6 58 PB7 59 PF1 6 BOOT0 60 PB8 61 PB9 62 VSS 63 VDD 64 NRST 7 PC0 8 PC1 9 U1 STM32F303R6Tx 0.1u C36 GND

*Split termination improves the
electromagnetic emissions behavior of the network by eliminating fluctuations in the bus common mode voltages at the start and end of message transmissions LPF Cutoff f = 1/(2*pi*Rsplit*CSplit) = 564kHz

*Under normal operation pop. 1k instead of C18

1 RESET 10 SWDIO/TMS 2 GND
J6 OLED VCC

3 SWDCLK/TCK 4 SWO/TDO 6 NC/TDI 8 GNDDetect 9

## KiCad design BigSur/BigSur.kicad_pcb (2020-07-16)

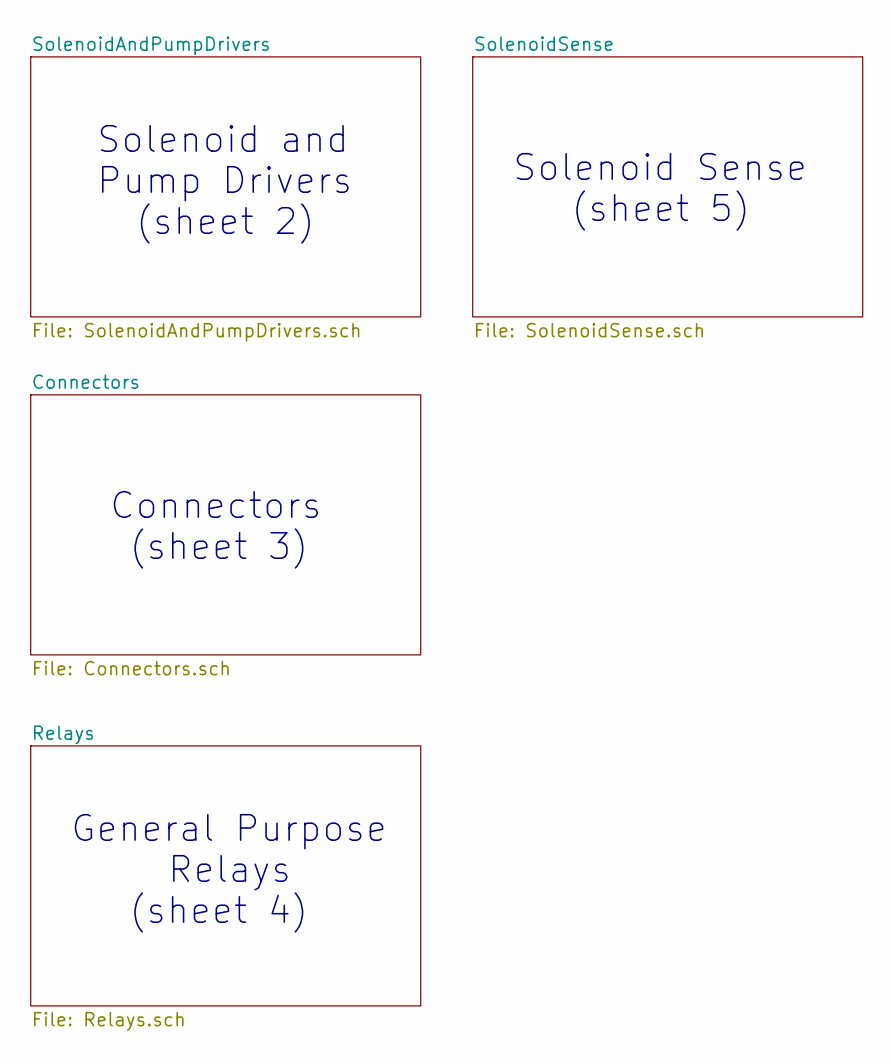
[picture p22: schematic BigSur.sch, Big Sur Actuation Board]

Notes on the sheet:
Connectors (sheet 3)
General Purpose Relays (sheet 4)
Solenoid and Pump Drivers (sheet 2)
Solenoid Sense (sheet 5)

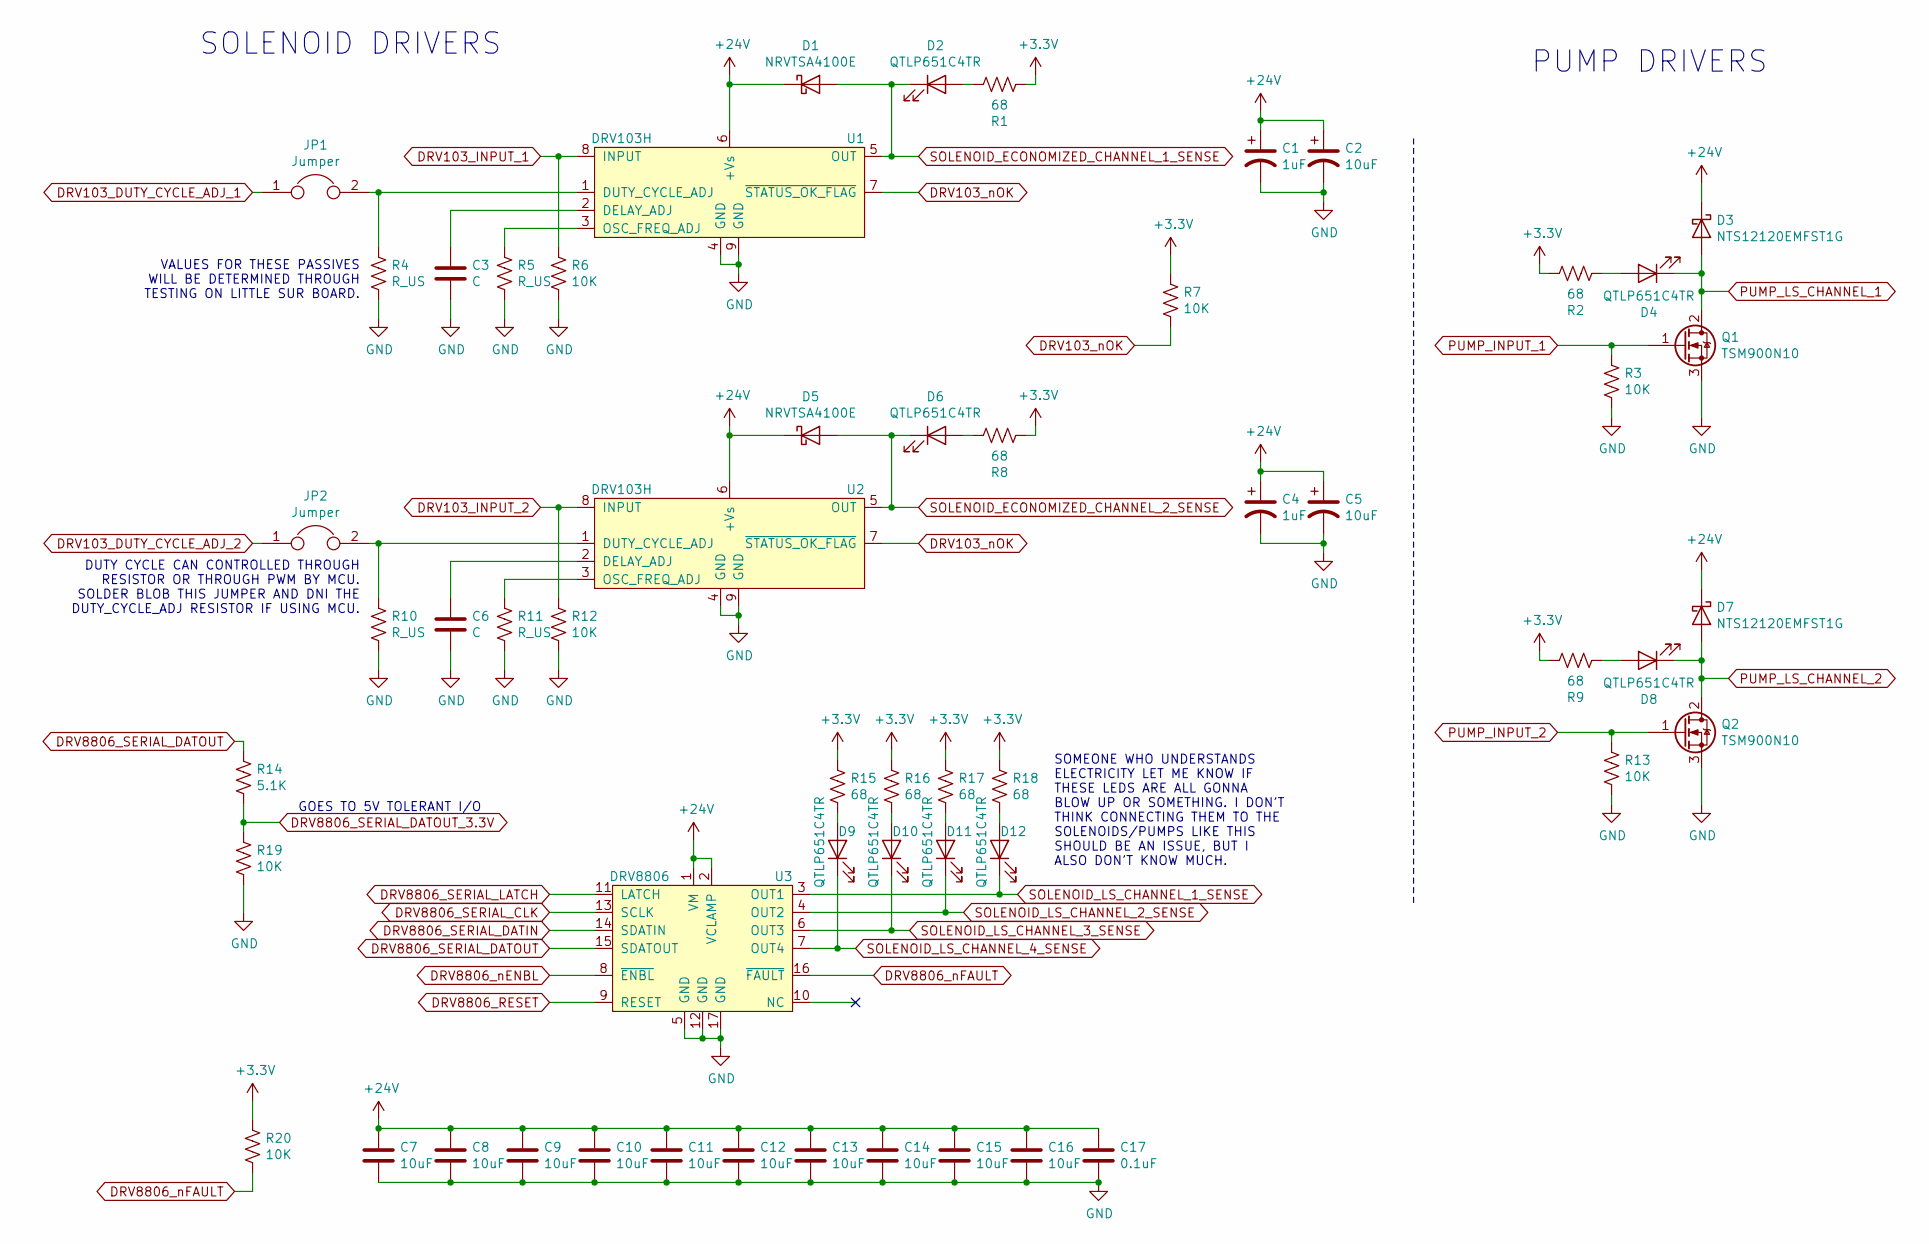
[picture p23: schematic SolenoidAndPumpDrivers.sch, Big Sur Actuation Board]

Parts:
C1, C4: 1uF; KEMET_CAP_SMD_T491C105K050AT; Part Number T491C105K050AT
C2, C5: 10uF; VISHAY_CAP_SMD_293D106X9050E2TE3; Part Number 293D106X9050E2TE3
C3, C6: C; C_1210_3225Metric_Pad1.42x2.65mm_HandSolder
C7, C8, C9, C10, C11, C12, C13, C14, C15, C16: 10uF; C_1210_3225Metric_Pad1.42x2.65mm_HandSolder; Part Number UMK325BJ106KMHP
C17: 0.1uF; C_0603_1608Metric_Pad1.05x0.95mm_HandSolder; Part Number CL10B104KB8NNNC
D1, D5: NRVTSA4100E; ONSemi_SMD_Schottky_NRVTSA4100E
D2, D4, D6, D8, D9, D10, D11, D12: QTLP651C4TR; LED_1206_3216Metric_Pad1.42x1.75mm_HandSolder
D3, D7: NTS12120EMFST1G; ONSemi_SMD_Schottky_NTS12120EMFS
JP1, JP2: Jumper; SolderJumper-2_P1.3mm_Open_RoundedPad1.0x1.5mm
Q1, Q2: TSM900N10; TO-252-2
R1, R2, R8, R9, R15, R16, R17, R18: 68; R_0603_1608Metric_Pad1.05x0.95mm_HandSolder; Part Number ESR03EZPJ680
R3, R6, R7, R12, R13, R19, R20: 10K; R_0603_1608Metric_Pad1.05x0.95mm_HandSolder; Part Number RNCP0603FTD10K0
R4, R5, R10, R11: R_US; R_1210_3225Metric_Pad1.42x2.65mm_HandSolder
R14: 5.1K; R_0603_1608Metric_Pad1.05x0.95mm_HandSolder; Part Number CR0603-FX-5101ELF
U1, U2: DRV103H; SOIC-8-1EP_3.9x4.9mm_P1.27mm_EP2.29x3mm_ThermalVias
U3: DRV8806; HTSSOP-16-1EP_4.4x5mm_P0.65mm_EP3.4x5mm_Mask2.46x2.31mm_The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

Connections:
+3V3: R1.2, R2.1, R7.1, R8.2, R9.1, R15.1, R16.1, R17.1, R18.1, R20.1; also elsewhere on the board
+24V: C1.1, C2.1, C4.1, C5.1, C7.1, C8.1, C9.1, C10.1, C11.1, C12.1, C13.1, C14.1, C15.1, C16.1, C17.1, D1.1 (K), D3.1 (K), D5.1 (K), D7.1 (K), U1.6 (+Vs), U2.6 (+Vs), U3.1 (VM), U3.2 (VCLAMP); also elsewhere on the board
DRV103_DUTY_CYCLE_ADJ_1: JP1.1; also elsewhere on the board
DRV103_DUTY_CYCLE_ADJ_2: JP2.1; also elsewhere on the board
DRV103_INPUT_1: R6.1, U1.8 (INPUT); also elsewhere on the board
DRV103_INPUT_2: R12.1, U2.8 (INPUT); also elsewhere on the board
DRV103_nOK: R7.2, U1.7 (~STATUS_OK_FLAG~), U2.7 (~STATUS_OK_FLAG~); also elsewhere on the board
DRV8806_RESET: U3.9 (RESET); also elsewhere on the board
DRV8806_SERIAL_CLK: U3.13 (SCLK); also elsewhere on the board
DRV8806_SERIAL_DATIN: U3.14 (SDATIN); also elsewhere on the board
DRV8806_SERIAL_DATOUT: R14.1, U3.15 (SDATOUT)
DRV8806_SERIAL_DATOUT_3.3V: R14.2, R19.1; also elsewhere on the board
DRV8806_SERIAL_LATCH: U3.11 (LATCH); also elsewhere on the board
DRV8806_nENBL: U3.8 (~ENBL~); also elsewhere on the board
DRV8806_nFAULT: R20.2, U3.16 (~FAULT~); also elsewhere on the board
GND: C1.2, C2.2, C3.2, C4.2, C5.2, C6.2, C7.2, C8.2, C9.2, C10.2, C11.2, C12.2, C13.2, C14.2, C15.2, C16.2, C17.2, Q1.3 (S), Q2.3 (S), R3.2, R4.2, R5.2, R6.2, R10.2, R11.2, R12.2, R13.2, R19.2, U1.4 (GND), U1.9 (GND), U2.4 (GND), U2.9 (GND), U3.5 (GND), U3.12 (GND), U3.17 (GND); also elsewhere on the board
unnamed: C3.1, U1.2 (DELAY_ADJ)
unnamed: C6.1, U2.2 (DELAY_ADJ)
unnamed: D2.2 (A), R1.1
unnamed: D4.2 (A), R2.2
unnamed: D6.2 (A), R8.1
unnamed: D8.2 (A), R9.2
unnamed: D9.2 (A), R15.2
unnamed: D10.2 (A), R16.2
unnamed: D11.2 (A), R17.2
unnamed: D12.2 (A), R18.2
unnamed: JP1.2, R4.1, U1.1 (DUTY_CYCLE_ADJ)
unnamed: JP2.2, R10.1, U2.1 (DUTY_CYCLE_ADJ)
unnamed: R5.1, U1.3 (OSC_FREQ_ADJ)
unnamed: R11.1, U2.3 (OSC_FREQ_ADJ)
PUMP_INPUT_1: Q1.1 (G), R3.1; also elsewhere on the board
PUMP_INPUT_2: Q2.1 (G), R13.1; also elsewhere on the board
PUMP_LS_CHANNEL_1: D3.2 (A), D4.1 (K), Q1.2 (D); also elsewhere on the board
PUMP_LS_CHANNEL_2: D7.2 (A), D8.1 (K), Q2.2 (D); also elsewhere on the board
SOLENOID_ECONOMIZED_CHANNEL_1_SENSE: D1.2 (A), D2.1 (K), U1.5 (OUT); also elsewhere on the board
SOLENOID_ECONOMIZED_CHANNEL_2_SENSE: D5.2 (A), D6.1 (K), U2.5 (OUT); also elsewhere on the board
SOLENOID_LS_CHANNEL_1_SENSE: D12.1 (K), U3.3 (OUT1); also elsewhere on the board
SOLENOID_LS_CHANNEL_2_SENSE: D11.1 (K), U3.4 (OUT2); also elsewhere on the board
SOLENOID_LS_CHANNEL_3_SENSE: D10.1 (K), U3.6 (OUT3); also elsewhere on the board
SOLENOID_LS_CHANNEL_4_SENSE: D9.1 (K), U3.7 (OUT4); also elsewhere on the board

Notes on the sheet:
VALUES FOR THESE PASSIVES WILL BE DETERMINED THROUGH TESTING ON LITTLE SUR BOARD.
DUTY CYCLE CAN CONTROLLED THROUGH RESISTOR OR THROUGH PWM BY MCU. SOLDER BLOB THIS JUMPER AND DNI THE DUTY_CYCLE_ADJ RESISTOR IF USING MCU.
SOMEONE WHO UNDERSTANDS ELECTRICITY LET ME KNOW IF THESE LEDS ARE ALL GONNA BLOW UP OR SOMETHING. I DON’T THINK CONNECTING THEM TO THE SOLENOIDS/PUMPS LIKE THIS SHOULD BE AN ISSUE, BUT I ALSO DON’T KNOW MUCH.
GOES TO 5V TOLERANT I/O
SOLENOID DRIVERS
PUMP DRIVERS

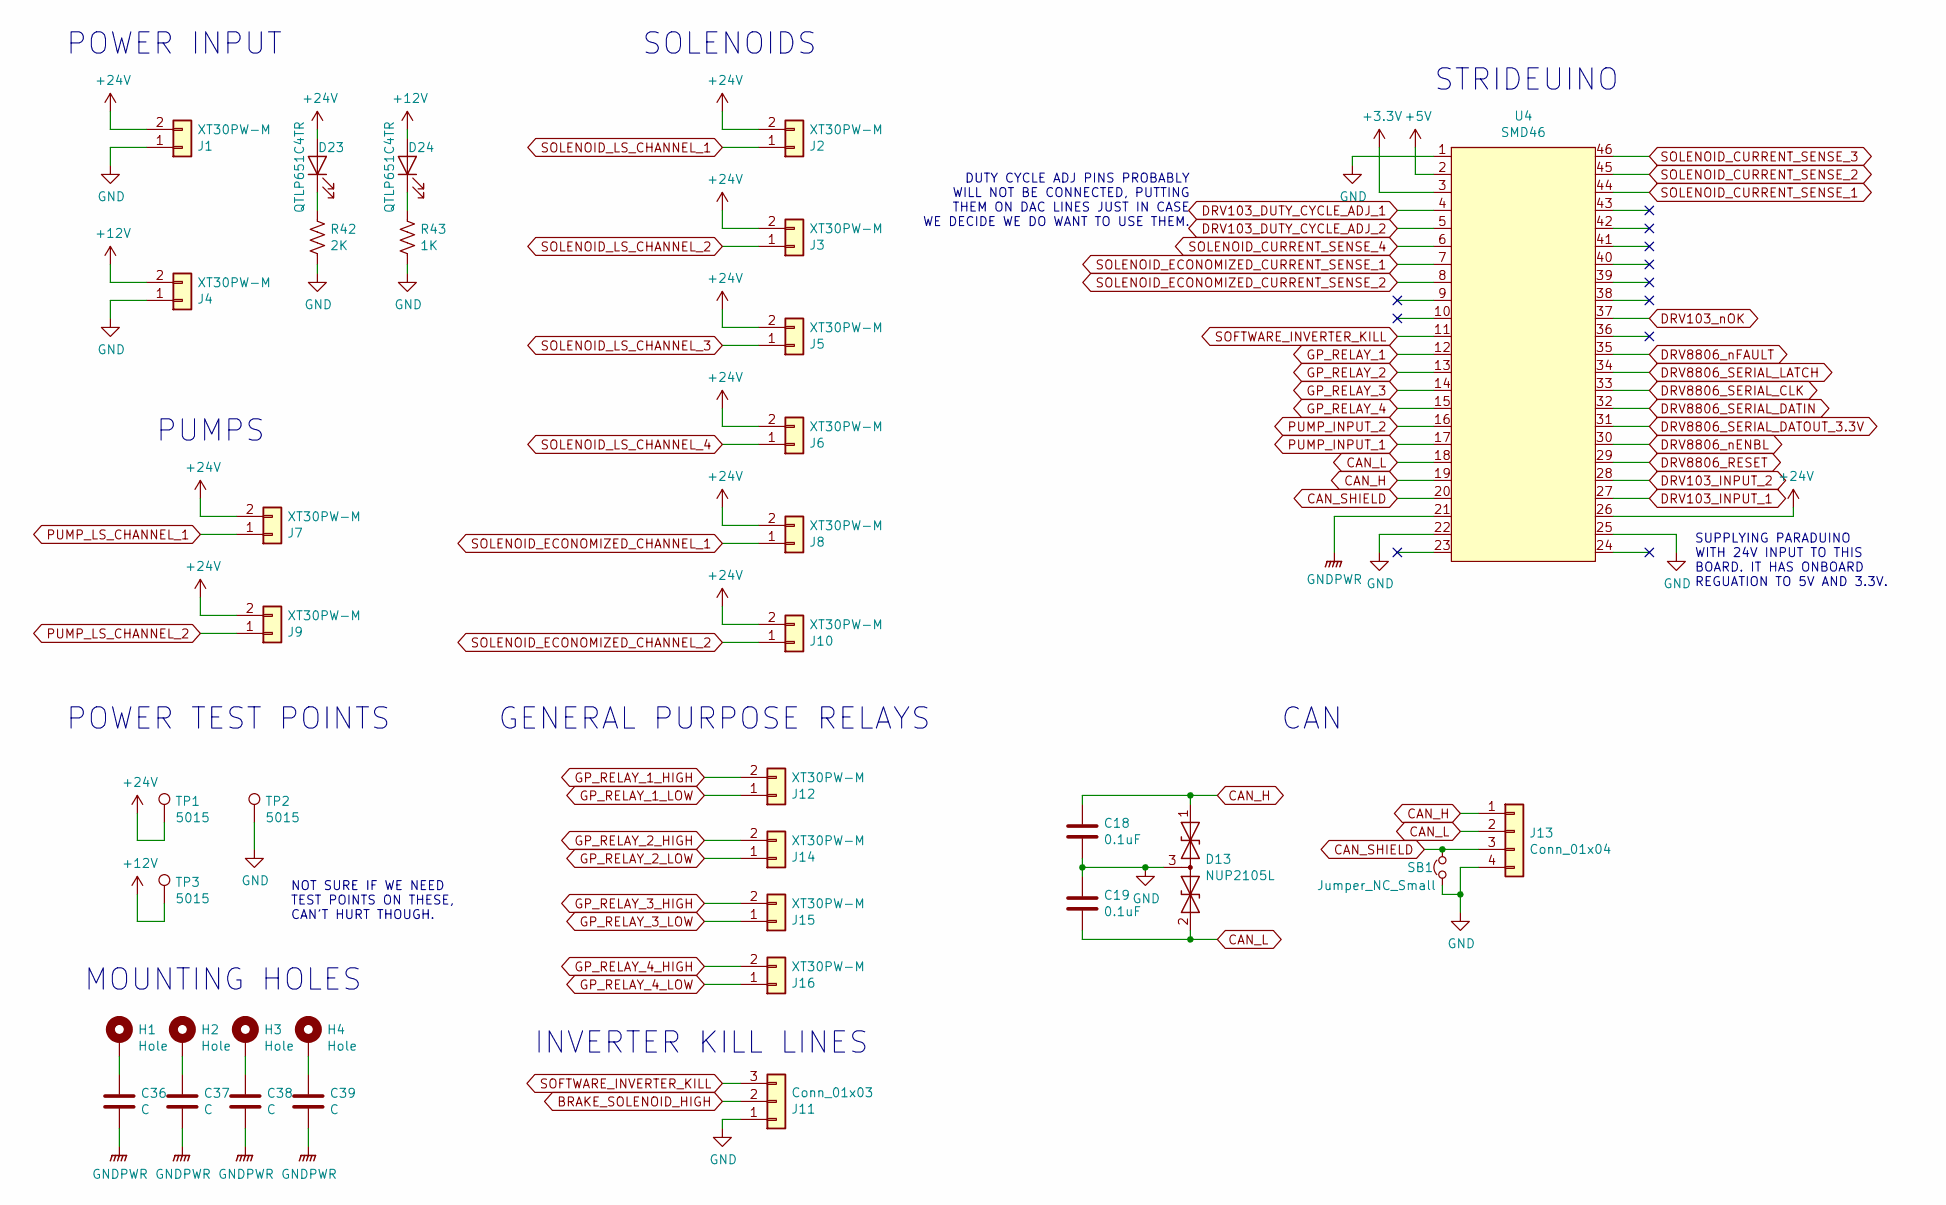
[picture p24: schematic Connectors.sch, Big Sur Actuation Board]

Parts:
C18, C19: 0.1uF; C_0603_1608Metric_Pad1.05x0.95mm_HandSolder; Part Number CL10B104KB8NNNC
C36, C37, C38, C39: C; C_0603_1608Metric_Pad1.05x0.95mm_HandSolder
D13: NUP2105L; SOT-23
D23, D24: QTLP651C4TR; LED_1206_3216Metric_Pad1.42x1.75mm_HandSolder
H1, H2, H3, H4: Hole; MountingHole_4.3mm_M4_Pad
J1, J2, J3, J4, J5, J6, J7, J8, J9, J10, J12, J14, J15, J16: XT30PW-M; AMASS_XT30PW-M
J11: Conn_01x03
J13: Conn_01x04
R42: 2K; R_0603_1608Metric_Pad1.05x0.95mm_HandSolder; Part Number ESR03EZPJ202
R43: 1K; R_0603_1608Metric_Pad1.05x0.95mm_HandSolder; Part Number RMCF0603JJ1K00
SB1: Jumper_NC_Small; SolderJumper-2_P1.3mm_Open_RoundedPad1.0x1.5mm
TP1, TP2, TP3: 5015; Keystone_TP_SMD_5015
U4: SMD46; SMD42-FTP

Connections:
+3V3: U4.3; also elsewhere on the board
+5V: U4.2
+12V: D24.2 (A), J4.2, TP3.1; also elsewhere on the board
+24V: D23.2 (A), J1.2, J2.2, J3.2, J5.2, J6.2, J7.2, J8.2, J9.2, J10.2, TP1.1, U4.26; also elsewhere on the board
CAN_H: C18.1, D13.1 (A1), J13.1, U4.19
CAN_L: C19.2, D13.2 (A2), J13.2, U4.18
CAN_SHIELD: J13.3, SB1.2, U4.20
DRV103_DUTY_CYCLE_ADJ_1: U4.4; also elsewhere on the board
DRV103_DUTY_CYCLE_ADJ_2: U4.5; also elsewhere on the board
DRV103_INPUT_1: U4.27; also elsewhere on the board
DRV103_INPUT_2: U4.28; also elsewhere on the board
DRV103_nOK: U4.37; also elsewhere on the board
DRV8806_RESET: U4.29; also elsewhere on the board
DRV8806_SERIAL_CLK: U4.33; also elsewhere on the board
DRV8806_SERIAL_DATIN: U4.32; also elsewhere on the board
DRV8806_SERIAL_DATOUT_3.3V: U4.31; also elsewhere on the board
DRV8806_SERIAL_LATCH: U4.34; also elsewhere on the board
DRV8806_nENBL: U4.30; also elsewhere on the board
DRV8806_nFAULT: U4.35; also elsewhere on the board
GND: C18.2, C19.1, D13.3 (common), J1.1, J4.1, J11.1, J13.4, R42.2, R43.2, SB1.1, TP2.1, U4.1, U4.22, U4.25; also elsewhere on the board
GNDPWR: C36.2, C37.2, C38.2, C39.2, U4.21
GP_RELAY_1: U4.12; also elsewhere on the board
GP_RELAY_1_HIGH: J12.2; also elsewhere on the board
GP_RELAY_1_LOW: J12.1; also elsewhere on the board
GP_RELAY_2: U4.13; also elsewhere on the board
GP_RELAY_2_HIGH: J14.2; also elsewhere on the board
GP_RELAY_2_LOW: J14.1; also elsewhere on the board
GP_RELAY_3: U4.14; also elsewhere on the board
GP_RELAY_3_HIGH: J15.2; also elsewhere on the board
GP_RELAY_3_LOW: J15.1; also elsewhere on the board
GP_RELAY_4: U4.15; also elsewhere on the board
GP_RELAY_4_HIGH: J16.2; also elsewhere on the board
GP_RELAY_4_LOW: J16.1; also elsewhere on the board
unnamed: C36.1, H1.1
unnamed: C37.1, H2.1
unnamed: C38.1, H3.1
unnamed: C39.1, H4.1
unnamed: D23.1 (K), R42.1
unnamed: D24.1 (K), R43.1
PUMP_INPUT_1: U4.17; also elsewhere on the board
PUMP_INPUT_2: U4.16; also elsewhere on the board
PUMP_LS_CHANNEL_1: J7.1; also elsewhere on the board
PUMP_LS_CHANNEL_2: J9.1; also elsewhere on the board
SOFTWARE_INVERTER_KILL: J11.3, U4.11
SOLENOID_CURRENT_SENSE_1: U4.44; also elsewhere on the board
SOLENOID_CURRENT_SENSE_2: U4.45; also elsewhere on the board
SOLENOID_CURRENT_SENSE_3: U4.46; also elsewhere on the board
SOLENOID_CURRENT_SENSE_4: U4.6; also elsewhere on the board
SOLENOID_ECONOMIZED_CHANNEL_1: J8.1; also elsewhere on the board
SOLENOID_ECONOMIZED_CHANNEL_2: J10.1; also elsewhere on the board
SOLENOID_ECONOMIZED_CURRENT_SENSE_1: U4.7; also elsewhere on the board
SOLENOID_ECONOMIZED_CURRENT_SENSE_2: U4.8; also elsewhere on the board
SOLENOID_LS_CHANNEL_1: J2.1; also elsewhere on the board
SOLENOID_LS_CHANNEL_2: J3.1; also elsewhere on the board
SOLENOID_LS_CHANNEL_3: J5.1; also elsewhere on the board
SOLENOID_LS_CHANNEL_4: J6.1; also elsewhere on the board

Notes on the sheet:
POWER INPUT
STRIDEUINO
SOLENOIDS
PUMPS
DUTY CYCLE ADJ PINS PROBABLY WILL NOT BE CONNECTED, PUTTING THEM ON DAC LINES JUST IN CASE WE DECIDE WE DO WANT TO USE THEM.
POWER TEST POINTS
NOT SURE IF WE NEED TEST POINTS ON THESE, CAN’T HURT THOUGH.
CAN
GENERAL PURPOSE RELAYS
MOUNTING HOLES
SUPPLYING PARADUINO WITH 24V INPUT TO THIS BOARD. IT HAS ONBOARD REGUATION TO 5V AND 3.3V.
INVERTER KILL LINES

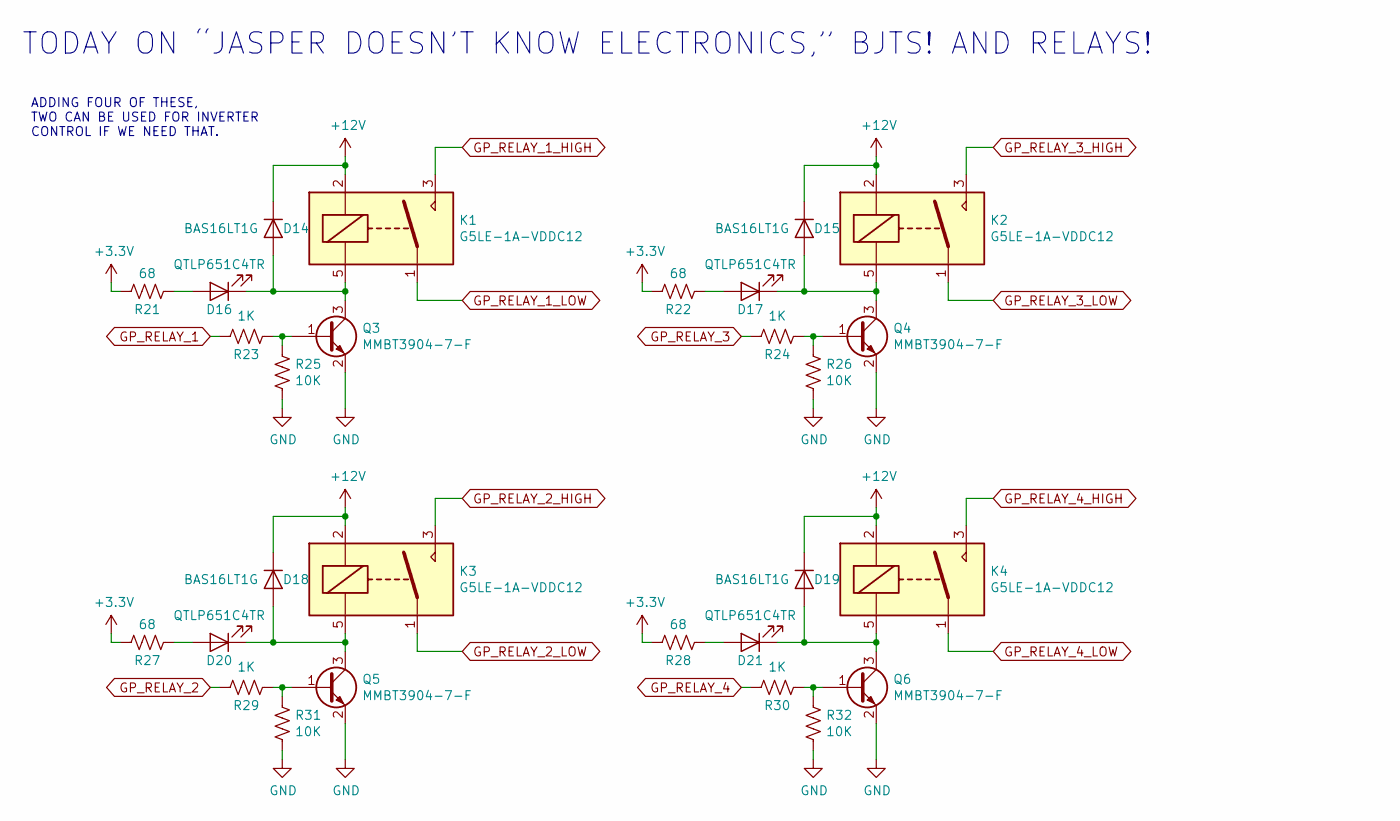
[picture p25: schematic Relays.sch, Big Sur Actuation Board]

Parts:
D14, D15, D18, D19: BAS16LT1G; SOT-23_Handsoldering
D16, D17, D20, D21: QTLP651C4TR; LED_1206_3216Metric_Pad1.42x1.75mm_HandSolder
K1, K2, K3, K4: G5LE-1A-VDDC12; OMRON_RELAY_G5LE-1A-VDDC12
Q3, Q4, Q5, Q6: MMBT3904-7-F; SOT-23_Handsoldering
R21, R22, R27, R28: 68; R_0603_1608Metric_Pad1.05x0.95mm_HandSolder; Part Number ESR03EZPJ680
R23, R24, R29, R30: 1K; R_0603_1608Metric_Pad1.05x0.95mm_HandSolder; Part Number RMCF0603JJ1K00
R25, R26, R31, R32: 10K; R_0603_1608Metric_Pad1.05x0.95mm_HandSolder; Part Number RNCP0603FTD10K0

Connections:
+3V3: R21.1, R22.1, R27.1, R28.1; also elsewhere on the board
+12V: D14.1 (K), D15.1 (K), D18.1 (K), D19.1 (K), K1.2, K2.2, K3.2, K4.2; also elsewhere on the board
GND: Q3.2 (E), Q4.2 (E), Q5.2 (E), Q6.2 (E), R25.2, R26.2, R31.2, R32.2; also elsewhere on the board
GP_RELAY_1: R23.2; also elsewhere on the board
GP_RELAY_1_HIGH: K1.3; also elsewhere on the board
GP_RELAY_1_LOW: K1.1; also elsewhere on the board
GP_RELAY_2: R29.2; also elsewhere on the board
GP_RELAY_2_HIGH: K3.3; also elsewhere on the board
GP_RELAY_2_LOW: K3.1; also elsewhere on the board
GP_RELAY_3: R24.2; also elsewhere on the board
GP_RELAY_3_HIGH: K2.3; also elsewhere on the board
GP_RELAY_3_LOW: K2.1; also elsewhere on the board
GP_RELAY_4: R30.2; also elsewhere on the board
GP_RELAY_4_HIGH: K4.3; also elsewhere on the board
GP_RELAY_4_LOW: K4.1; also elsewhere on the board
unnamed: D14.2 (A), D16.1 (K), K1.5, Q3.3 (C)
unnamed: D15.2 (A), D17.1 (K), K2.5, Q4.3 (C)
unnamed: D16.2 (A), R21.2
unnamed: D17.2 (A), R22.2
unnamed: D18.2 (A), D20.1 (K), K3.5, Q5.3 (C)
unnamed: D19.2 (A), D21.1 (K), K4.5, Q6.3 (C)
unnamed: D20.2 (A), R27.2
unnamed: D21.2 (A), R28.2
unnamed: Q3.1 (B), R23.1, R25.1
unnamed: Q4.1 (B), R24.1, R26.1
unnamed: Q5.1 (B), R29.1, R31.1
unnamed: Q6.1 (B), R30.1, R32.1

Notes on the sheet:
TODAY ON “JASPER DOESN’T KNOW ELECTRONICS,” BJTS! AND RELAYS!
ADDING FOUR OF THESE, TWO CAN BE USED FOR INVERTER CONTROL IF WE NEED THAT.

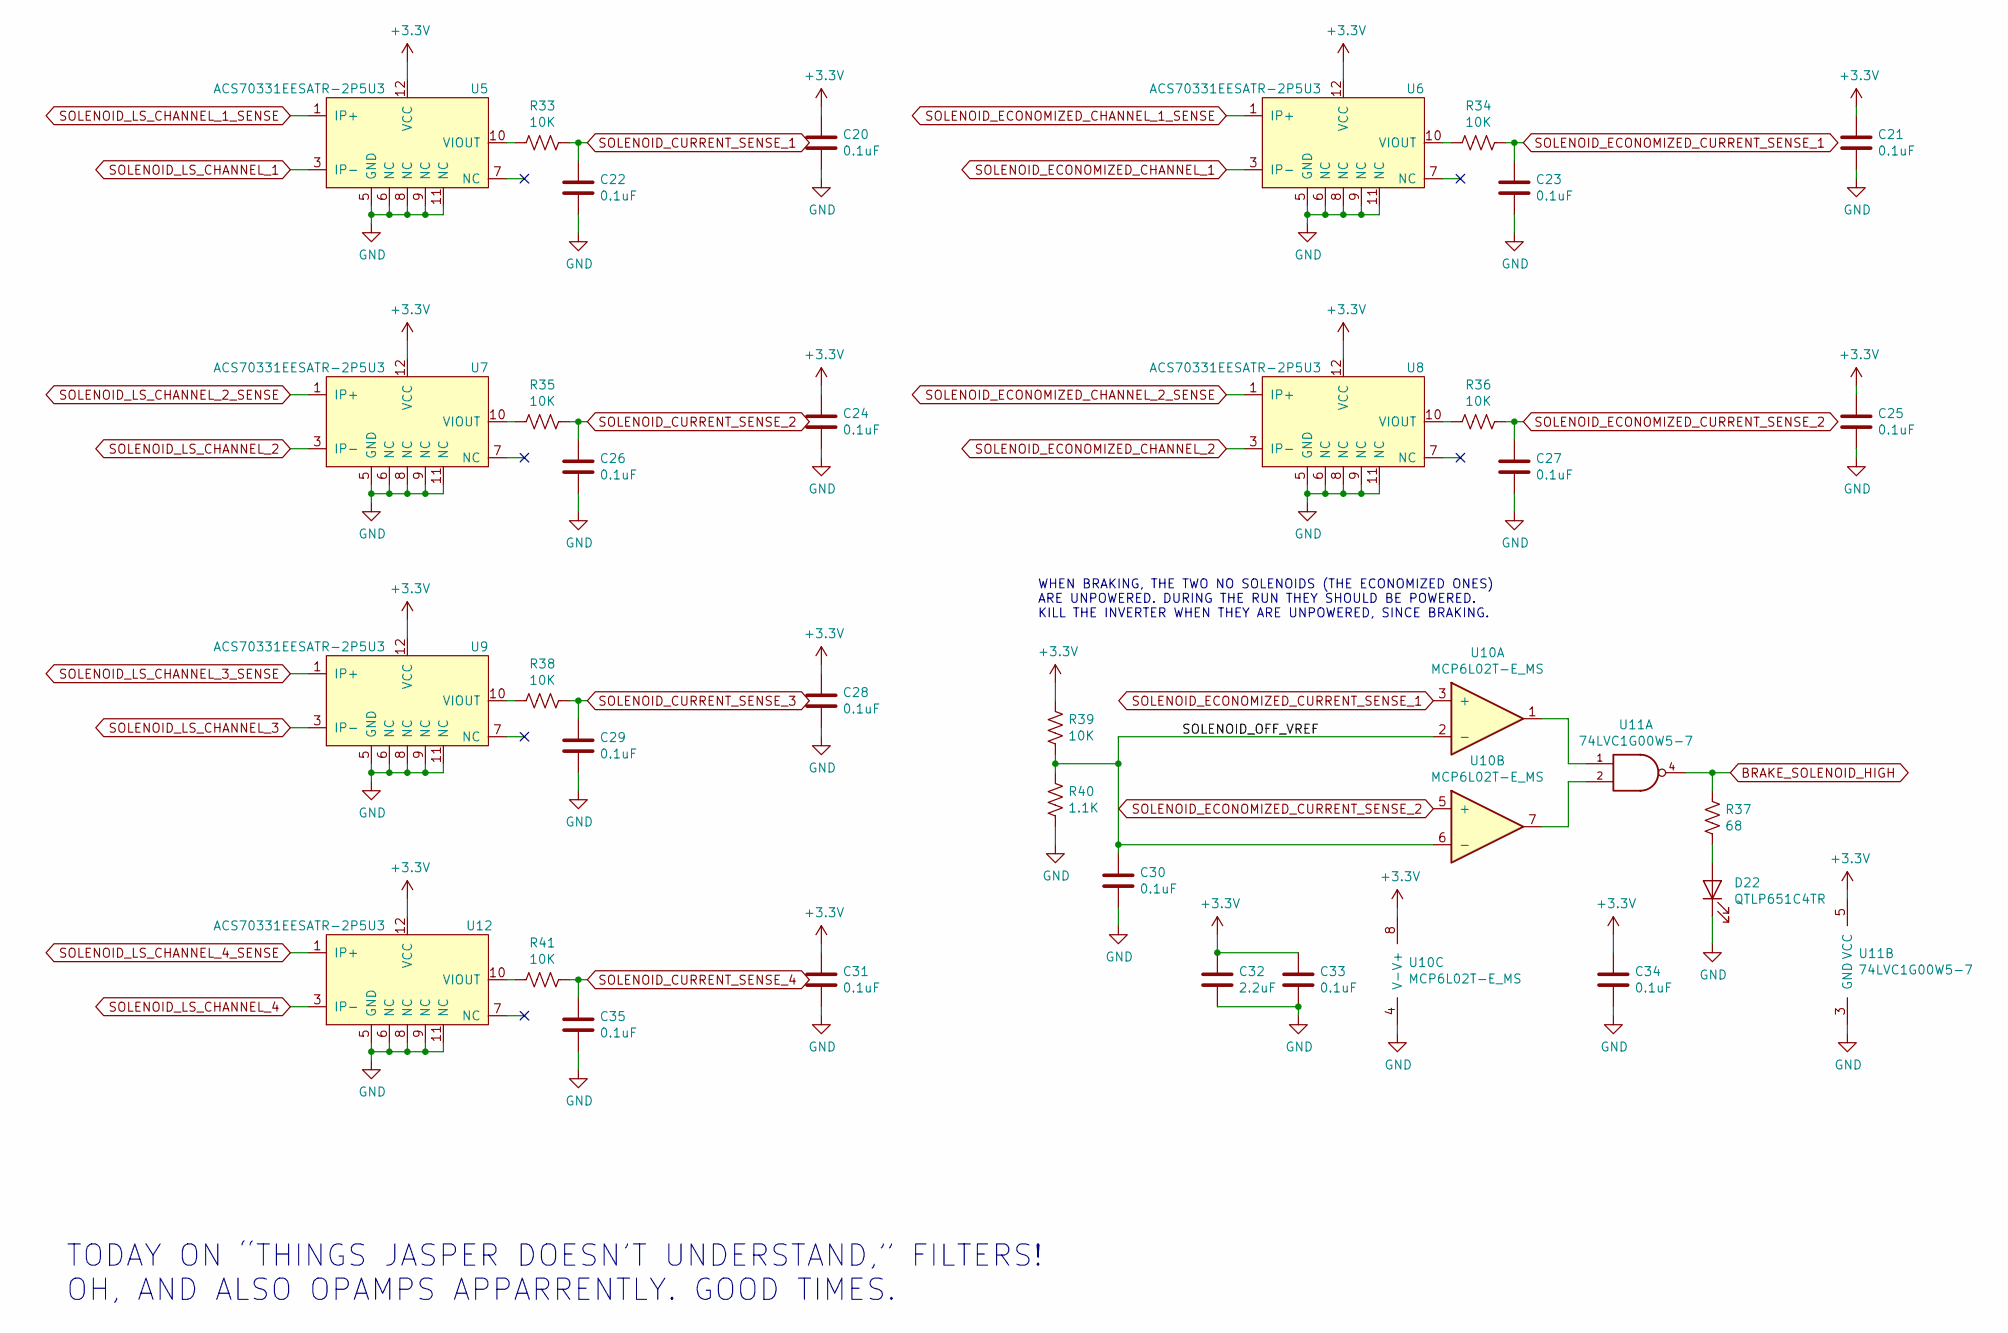
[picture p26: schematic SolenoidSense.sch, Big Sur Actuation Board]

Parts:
C20, C21, C22, C23, C24, C25, C26, C27, C28, C29, C30, C31, C33, C34, C35: 0.1uF; C_0603_1608Metric_Pad1.05x0.95mm_HandSolder; Part Number CL10B104KB8NNNC
C32: 2.2uF; C_0603_1608Metric_Pad1.05x0.95mm_HandSolder; Part Number CL10B104KB8NNNC
D22: QTLP651C4TR; LED_1206_3216Metric_Pad1.42x1.75mm_HandSolder
R33, R34, R35, R36, R38, R39, R41: 10K; R_0603_1608Metric_Pad1.05x0.95mm_HandSolder; Part Number RNCP0603FTD10K0
R37: 68; R_0603_1608Metric_Pad1.05x0.95mm_HandSolder; Part Number ESR03EZPJ680
R40: 1.1K; R_0603_1608Metric_Pad1.05x0.95mm_HandSolder; Part Number RMCF0603FT1K10
U5, U6, U7, U8, U9, U12: ACS70331EESATR-2P5U3; Allegro_QFN_ACS70331EESATR
U10: MCP6L02T-E_MS; MSOP-8_3x3mm_P0.65mm; Digikey digikey.ca/product-detail/en/microchip-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
U11: 74LVC1G00W5-7; SOT-23-5

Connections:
+3V3: C20.1, C21.1, C24.1, C25.1, C28.1, C31.1, C32.1, C33.1, C34.1, R39.1, U5.12 (VCC), U6.12 (VCC), U7.12 (VCC), U8.12 (VCC), U9.12 (VCC), U10.8 (V+), U11.5 (VCC), U12.12 (VCC); also elsewhere on the board
/SolenoidSense/SOLENOID_OFF_VREF: C30.1, R39.2, R40.1, U10.2 (-), U10.6 (-)
BRAKE_SOLENOID_HIGH: R37.1, U11.4
GND: C20.2, C21.2, C22.2, C23.2, C24.2, C25.2, C26.2, C27.2, C28.2, C29.2, C30.2, C31.2, C32.2, C33.2, C34.2, C35.2, D22.1 (K), R40.2, U5.5 (GND), U5.6 (NC), U5.8 (NC), U5.9 (NC), U5.11 (NC), U6.5 (GND), U6.6 (NC), U6.8 (NC), U6.9 (NC), U6.11 (NC), U7.5 (GND), U7.6 (NC), U7.8 (NC), U7.9 (NC), U7.11 (NC), U8.5 (GND), U8.6 (NC), U8.8 (NC), U8.9 (NC), U8.11 (NC), U9.5 (GND), U9.6 (NC), U9.8 (NC), U9.9 (NC), U9.11 (NC), U10.4 (V-), U11.3 (GND), U12.5 (GND), U12.6 (NC), U12.8 (NC), U12.9 (NC), U12.11 (NC); also elsewhere on the board
unnamed: D22.2 (A), R37.2
unnamed: R33.2, U5.10 (VIOUT)
unnamed: R34.2, U6.10 (VIOUT)
unnamed: R35.2, U7.10 (VIOUT)
unnamed: R36.2, U8.10 (VIOUT)
unnamed: R38.2, U9.10 (VIOUT)
unnamed: R41.2, U12.10 (VIOUT)
unnamed: U10.1, U11.1
unnamed: U10.7, U11.2
SOLENOID_CURRENT_SENSE_1: C22.1, R33.1; also elsewhere on the board
SOLENOID_CURRENT_SENSE_2: C26.1, R35.1; also elsewhere on the board
SOLENOID_CURRENT_SENSE_3: C29.1, R38.1; also elsewhere on the board
SOLENOID_CURRENT_SENSE_4: C35.1, R41.1; also elsewhere on the board
SOLENOID_ECONOMIZED_CHANNEL_1: U6.3 (IP-); also elsewhere on the board
SOLENOID_ECONOMIZED_CHANNEL_1_SENSE: U6.1 (IP+); also elsewhere on the board
SOLENOID_ECONOMIZED_CHANNEL_2: U8.3 (IP-); also elsewhere on the board
SOLENOID_ECONOMIZED_CHANNEL_2_SENSE: U8.1 (IP+); also elsewhere on the board
SOLENOID_ECONOMIZED_CURRENT_SENSE_1: C23.1, R34.1, U10.3 (+); also elsewhere on the board
SOLENOID_ECONOMIZED_CURRENT_SENSE_2: C27.1, R36.1, U10.5 (+); also elsewhere on the board
SOLENOID_LS_CHANNEL_1: U5.3 (IP-); also elsewhere on the board
SOLENOID_LS_CHANNEL_1_SENSE: U5.1 (IP+); also elsewhere on the board
SOLENOID_LS_CHANNEL_2: U7.3 (IP-); also elsewhere on the board
SOLENOID_LS_CHANNEL_2_SENSE: U7.1 (IP+); also elsewhere on the board
SOLENOID_LS_CHANNEL_3: U9.3 (IP-); also elsewhere on the board
SOLENOID_LS_CHANNEL_3_SENSE: U9.1 (IP+); also elsewhere on the board
SOLENOID_LS_CHANNEL_4: U12.3 (IP-); also elsewhere on the board
SOLENOID_LS_CHANNEL_4_SENSE: U12.1 (IP+); also elsewhere on the board

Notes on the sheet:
TODAY ON “THINGS JASPER DOESN’T UNDERSTAND,” FILTERS! OH, AND ALSO OPAMPS APPARRENTLY. GOOD TIMES.
WHEN BRAKING, THE TWO NO SOLENOIDS (THE ECONOMIZED ONES) ARE UNPOWERED. DURING THE RUN THEY SHOULD BE POWERED. KILL THE INVERTER WHEN THEY ARE UNPOWERED, SINCE BRAKING.

Board: 2 copper layers, 152 parts (79 on the bottom side), 98 nets, no tracks yet.

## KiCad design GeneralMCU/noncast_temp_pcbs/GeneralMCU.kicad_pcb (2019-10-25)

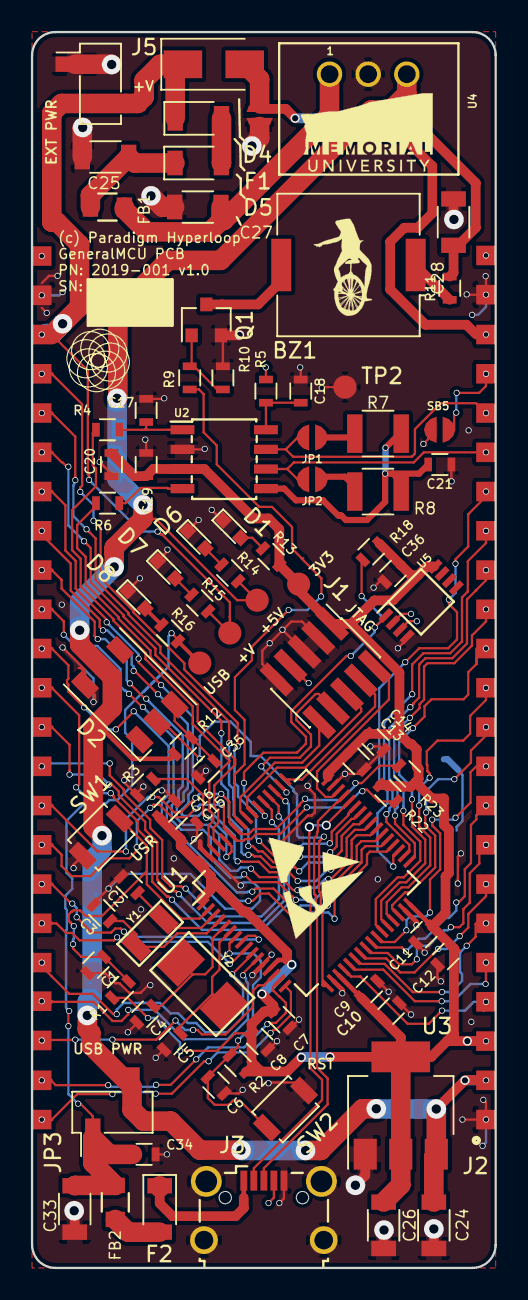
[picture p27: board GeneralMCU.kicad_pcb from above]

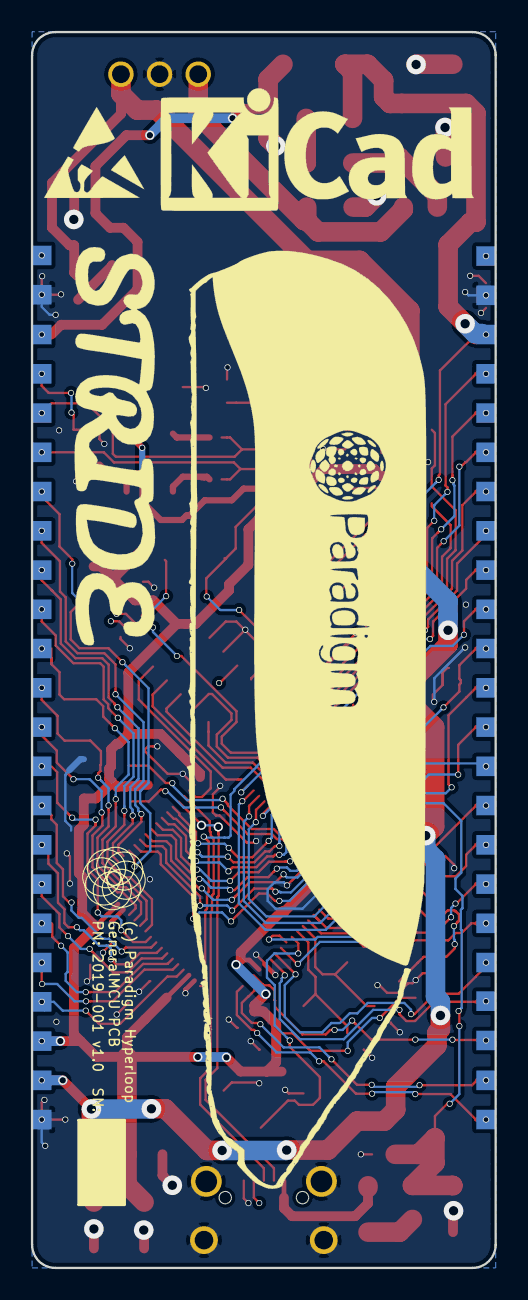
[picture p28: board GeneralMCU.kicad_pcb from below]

Board: 2 copper layers, 30.0 x 80.0 mm, 96 parts (6 on the bottom side), 81 nets.

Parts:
BZ1: Buzzer; Buzzer_Murata_PKMCS0909E4000-R1
C1, C6, C7, C9, C11, C13, C15, C18, C19, C36: 0.1u; SMD_pkg_0603
C2, C3: 13p; SMD_pkg_0603
C4, C5: 8p; SMD_pkg_0603
C8: 10n; SMD_pkg_0603
C10, C12, C14, C16, C20, C34, C35: 1u; SMD_pkg_0603
C17: DNP; SMD_pkg_0603
C21: 4.7n; SMD_pkg_0603
C24, C26: 1u; SMD_pkg_1206
C25, C27, C33: 10u; SMD_pkg_1206
C28: 22u; SMD_pkg_1206
D1: 3V3; LED_0603
D2: WS2812B; LED_WS2812-PLCC6
D4: D_TVS; D_SMA
D5: 40V 1A; D_1206
D6: 5V; LED_0603
D7: +V; LED_0603
D8: USB; LED_0603
F1: 3VDC 1A PTC; D_1206
F2: 500mA PTC; D_1206
FB1, FB2: FB; SMD_pkg_0805
J1: ARM_JTAG_SWD; PinHeader_2x05_P1.27mm_Vertical_SMD
J2: SMD46 castellation PKG; PAD42
J3: USB_B_Micro; USB_Micro-B_Wuerth-629105150521_CircularHoles
J5: PWR; Pin_Header_Straight_1x02_Pitch2.54mm_SMD_Pin1Left
JP1, JP2: Jumper_NC_Small; JUMPER_EGG
JP3: Jumper_NC_Small; Pin_Header_Straight_1x02_Pitch2.54mm_SMD_Pin1Left
Q1: Q_NMOS_DGS; SOT-23
R1, R2, R3, R12, R13, R14, R15, R16: 10k; SMD_pkg_0603
R4, R6, R11: 0; SMD_pkg_0603
R5: DNP; SMD_pkg_0603
R7, R8: 60; SMD_pkg_1210
R9, R10: 1k; SMD_pkg_0603
R18, R22, R23: 4.7k; SMD_pkg_0603
SB5, SB6: Jumper_NC_Small; JUMPER_EGG
SW1: USER; SW_SPST_B3U-1000P
SW2: RESET; SW_SPST_B3U-1000P
TP1: 3V3; Measurement_Point_Round-SMD-Pad_Small
TP2: GND; Measurement_Point_Round-SMD-Pad_Small
TP3: 5V; Measurement_Point_Round-SMD-Pad_Small
TP5: +V; Measurement_Point_Round-SMD-Pad_Small
TP6: USB; Measurement_Point_Round-SMD-Pad_Small
U1: STM32F303R6Tx; LQFP-64_10x10mm_Pitch0.5mm
U2: SN65HVD230; SOIC-8_N
U3: AZ1117-3.3; SOT-223-3_TabPin2
U4: P78E05-1000; Recom_INNOLINE-R-78E
U5: DS18B20; MSOP-8
Y1: 32.768kHz; Crystal_NDK_NX3215SA
Y2: 8MHz; Crystal_L5_W3.2
snblock1, snblock2: Logo_Open_Hardware_Small; SN_BLOCK
snblock3, snblock8: Logo_Open_Hardware_Small; Paradigm_Logo_Very_Small
snblock4: Logo_Open_Hardware_Small; poddy
snblock5: Logo_Open_Hardware_Small; KiCad-Logo_8mm_SilkScreen
snblock6, snblock7: Logo_Open_Hardware_Small; ESD-Logo_6.6x6mm_SilkScreen
snblock9: Logo_Open_Hardware_Small; datboi
snblock10: Logo_Open_Hardware_Small; stride
snblock11: Logo_Open_Hardware_Small; MUN

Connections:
+3V3: C7.1, C8.1, C9.1, C10.1, C11.1, C12.1, C13.1, C14.1, C15.1, C16.1, C19.1, C20.1, C26.1, C36.2, J1.1, J2.3, R1.2, R2.2, R13.2, R18.2, R22.2, R23.2, TP1.1, U1.1, U1.13, U1.19, U1.32, U1.48, U1.64, U2.3, U3.2, U5.8
+5V: C24.1, C28.1, D2.5, J2.2, JP3.2, R11.2, R12.2, R14.2, TP3.1, U3.3, U4.3
+V: D4.1, F1.1, J2.26, J5.2, R15.2, TP5.1
/BOOT0: R3.2, U1.60
/BUZZ: R9.1, U1.57
/CANH: J2.19, JP1.2, U2.7
/CANL: J2.18, JP2.2, U2.6
/CAN_RX: R6.1, U1.61
/CAN_Shield: J2.20, SB5.1
/CAN_TX: R4.1, U1.62
/I2C1_SCL: J2.38, R23.1, U1.58
/I2C1_SDA: J2.39, R22.1, U1.59
/JTAG_JTDI: J1.8, U1.50
/JTAG_JTDO: J1.6, U1.55
/JTAG_NJTRST: J1.10, U1.56
/JTAG_SWDCLK\TCK: J1.4, U1.49
/JTAG_SWDIO\TMS: J1.2, U1.46
/NRST: C6.1, R2.1, SW2.2, U1.7
/OSC32_IN: C2.1, U1.3, Y1.1
/OSC32_OUT: C3.1, U1.4, Y1.2
/OSC_IN: C4.1, U1.5, Y2.1
/OSC_OUT: C5.1, U1.6, Y2.2
/PA0: J2.44, U1.14
/PA1: J2.45, U1.15
/PA2: J2.46, U1.16
/PA4: J2.4, U1.20
/PA5: J2.5, U1.21
/PA6: J2.6, U1.22
/PA7: J2.7, U1.23
/PA8: J2.29, U1.41
/PA9: J2.28, U1.42
/PA10: J2.27, U1.43
/PB0: J2.10, U1.26
/PB1: J2.14, U1.27
/PB2: J2.13, U1.28
/PB10: J2.12, U1.29
/PB11: J2.11, U1.30
/PB12: J2.15, U1.33
/PB13: J2.16, U1.34
/PB14: J2.17, U1.35
/PB15: J2.34, U1.36
/PC0: J2.40, U1.8
/PC1: J2.41, U1.9
/PC2: J2.42, U1.10
/PC3: J2.43, U1.11
/PC4: J2.8, U1.24
/PC5: J2.9, U1.25
/PC6: J2.33, U1.37
/PC7: J2.32, U1.38
/PC8: J2.31, U1.39
/PC9: J2.30, U1.40
/PC10: J2.35, U1.51
/PC11: J2.36, U1.52
/PC12: J2.37, U1.53
/PC13: C1.1, R1.1, SW1.2, U1.2
/PD2: R18.1, U1.54, U5.1
/USB_DM: J3.2, U1.44
/USB_DP: J3.3, U1.45
/USR_LED: D2.2, U1.17
/Vref: C21.2, R7.2, R8.1, U2.5
CHASSIS: D4.2, J2.21, SB6.2
GND: C1.2, C2.2, C3.2, C4.2, C5.2, C6.2, C7.2, C8.2, C9.2, C10.2, C11.2, C12.2, C13.2, C14.2, C15.2, C16.2, C17.1, C18.1, C19.2, C20.2, C21.1, C24.2, C25.2, C26.2, C27.2, C28.2, C33.2, C34.2, C35.2, C36.1, D1.1, D2.6, D6.1, D7.1, D8.1, J1.3, J1.5, J1.9, J2.1, J2.22, J2.25, J3.5, J3.6, J5.1, Q1.2, R3.1, R10.2, SB5.2, SB6.1, SW1.1, SW2.1, TP2.1, U1.12, U1.18, U1.31, U1.47, U1.63, U2.2, U3.1, U4.2, U5.4
unnamed: BZ1.1, R11.1
unnamed: BZ1.2, Q1.3
unnamed: C17.2, R4.2, U2.1
unnamed: C18.2, R5.1, U2.8
unnamed: C25.1, D5.1, FB1.2
unnamed: C27.1, FB1.1, U4.1
unnamed: C35.1, D2.3, R12.1
unnamed: D1.2, R13.1
unnamed: D5.2, F1.2
unnamed: D6.2, R14.1
unnamed: D7.2, R15.1
unnamed: D8.2, R16.1
unnamed: F2.1, J3.1
unnamed: F2.2, FB2.2
unnamed: JP1.1, R7.1
unnamed: JP2.1, R8.2
unnamed: Q1.1, R9.2, R10.1
unnamed: R6.2, U2.4
VBUS: C33.1, C34.1, FB2.1, JP3.1, R16.2, TP6.1

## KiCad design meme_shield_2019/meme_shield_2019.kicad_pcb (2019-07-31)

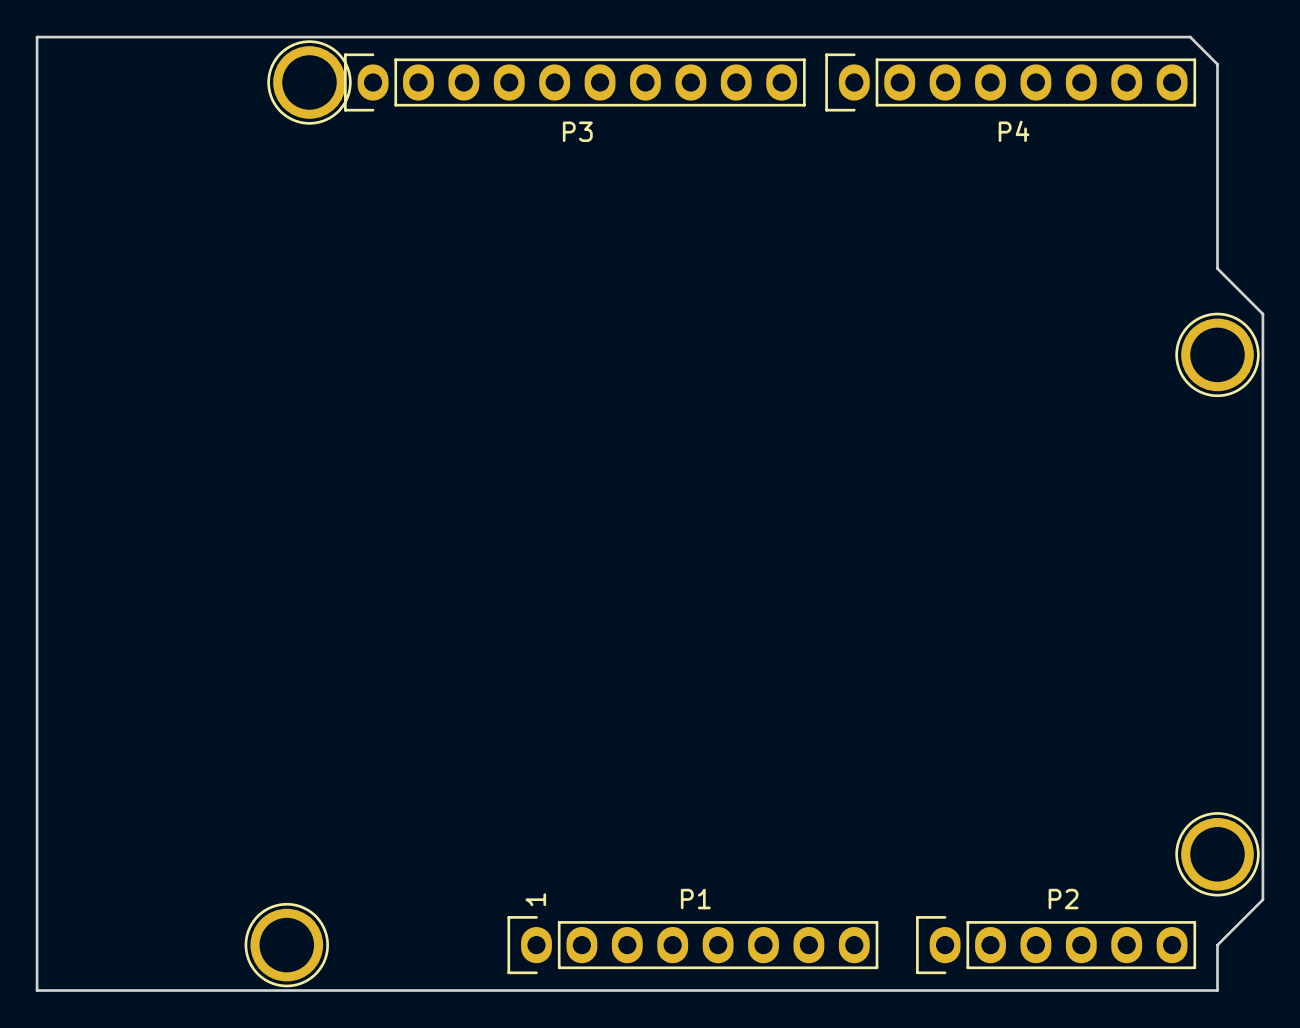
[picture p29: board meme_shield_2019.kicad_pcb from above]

Board: 2 copper layers, 68.6 x 53.3 mm, 15 parts (0 on the bottom side), 3 nets, no tracks yet.

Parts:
P1: Power; Socket_Strip_Arduino_1x08
P2: Analog; Socket_Strip_Arduino_1x06
P3: Digital; Socket_Strip_Arduino_1x10
P4: Digital; Socket_Strip_Arduino_1x08
P5, P6, P7, P8: CONN_01X01; Arduino_1pin
logo1: meme; 14553 Cerise Ave Hawthorne, CA 90250
logo2: meme; Blocked
logo3: meme; ExplodingGT
logo4: meme; FLoko
logo5: meme; juul_logo
logo6: meme; juul_Silk
logo7: meme; TidePod_Silk

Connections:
/A4(SDA): P2.5, P3.2
/A5(SCL): P2.6, P3.1
GND: P1.6, P1.7, P3.4

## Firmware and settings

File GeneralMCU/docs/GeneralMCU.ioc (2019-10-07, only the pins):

Mcu.UserName=STM32F303RETx
PA0.Signal=ADC1_IN1
PA11.Signal=USB_DM
PA12.Signal=USB_DP
PA13.GPIO_Label=TMS
PA13.Signal=SYS_JTMS-SWDIO
PA14.GPIO_Label=TCK
PA14.Signal=SYS_JTCK-SWCLK
PA15.Signal=SYS_JTDI
PA2.GPIO_Label=USART_TX
PA2.Signal=USART2_TX
PA3.GPIO_Label=USART_RX
PA3.Signal=USART2_RX
PA4.Signal=COMP_DAC11_group
PA5.GPIO_Label=LD2 [Green Led]
PA5.Signal=GPIO_Output
PB13.Signal=SPI2_SCK
PB14.Signal=SPI2_MISO
PB15.Signal=SPI2_MOSI
PB3.Signal=SYS_JTDO-TRACESWO
PB4.Signal=SYS_NJTRST
PB6.Signal=I2C1_SCL
PB7.Signal=I2C1_SDA
PB8.Signal=CAN_RX
PB9.Signal=CAN_TX
PC13.GPIO_Label=B1 [Blue PushButton]
PC13.Signal=GPXTI13
PC14-OSC32_IN.Signal=RCC_OSC32_IN
PC15-OSC32_OUT.Signal=RCC_OSC32_OUT
PF0-OSC_IN.Signal=RCC_OSC_IN
PF1-OSC_OUT.Signal=RCC_OSC_OUT

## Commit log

2019-07-24 added meme cape sch
    [meme_shield_2019.kicad_pcb, meme_shield_2019.sch]
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2019-08-13 Plopped mcu onto schematic
    Nothing final here yet besides mcu, other parts will change.
    [GeneralMCU.kicad_pcb, GeneralMCU.sch]
2019-08-14 Schematic getting toasty.
    99% Percent of symbols added with 90% of footprints filled in, 30% of parts spec'd.
    Layout organized by functional group
    [GeneralMCU.kicad_pcb, GeneralMCU.sch]
2019-09-16 Needs castellated pads and sch review
    [GeneralMCU.kicad_pcb, GeneralMCU.sch]
2019-09-16 Initial commit of Big Sur (Actuation Board).
    Solenoid drivers and sense *mostly* complete, pump drivers started.
    [Big Sur.kicad_pcb, Big Sur.sch, Connectors.sch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]
2019-09-20 Work on pump drivers.
    [Big Sur.sch, Connectors.sch, PumpDrivers.sch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]
2019-09-23 Started filling in pinout of Paraduino connector, based on current Paraduino schematic.
    [Connectors.sch, PumpDrivers.sch]
2019-10-02 Updated current sense, second pump driver, solenoid connectors
    -Current sense now uses current sense ICs, connected to Paraduino ADC pins.
    -Added second pump driver.
    -Connected outputs with XT30 connectors.
    -Still need some Paraduino connections, inverter driver, footprints.
    [Big Sur.sch, Connectors.sch, PumpDrivers.sch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]
2019-10-03 Removed Inverter
    [Big Sur.sch, Connectors.sch, PumpDrivers.sch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]
2019-10-05 Schematics Complete
    Still need to spec resistors, and XT30s, then should be ready for layout and routing.
    [Connectors.sch, PumpDrivers.sch, SolenoidDrivers.sch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]
2019-10-05 Changed "Big Sur" to "BigSur" to fit more closely with KiCAD conventions.
    [BigSur.kicad_pcb, BigSur.sch, Connectors.sch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]
2019-10-07 Redid the layout of the board to be better
    Smaller 30x80mm footprint. Sch symbol and footprint for the board can be found under the example folder. Routing needs to be made nice yet.
    [GeneralMCU - Old Layout.kicad_pcb, GeneralMCU.kicad_pcb, GeneralMCU_Example.kicad_pcb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]
2019-10-08 Added test points, started CAN connector.
    [Connectors.sch, SolenoidDrivers.sch]
2019-10-08 Can't remember these changes lol
    From the meeting, switching back to branch now.
    [GeneralMCU.kicad_pcb, GeneralMCU.sch]
2019-10-09 Added mounting holes, CAN connector, indicator LEDs, started general purpose relays
    [BigSur.sch, Connectors.sch, PumpDrivers.sch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]
2019-10-10 Chose LEDs.
    [SolenoidAndPumpDrivers.sch]
2019-10-11 Fixed castellated pads. Ready for review
    [GeneralMCU.kicad_pcb, GeneralMCU.sch]
2019-10-12 Updated test points
    [Connectors.sch, Relays.sch, SolenoidAndPumpDrivers.sch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]
2019-10-13 Added silk and generated gerbers. Review me.
    [GeneralMCU-B_Cu.gbr, GeneralMCU-B_Mask.gbr, GeneralMCU-B_Paste.gbr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]
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2019-10-13 Updated Example project and smd sym and footprint for recieving pcbs.
    [GeneralMCU_Example.kicad_pcb, GeneralMCU_Example.sch]
2019-10-17 Added braking detection, relay flyback, changed current sensors.
    [Connectors.sch, Relays.sch, SolenoidAndPumpDrivers.sch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]
2019-10-17 Added to self deprecation.
    [SolenoidSense.sch]
2019-10-18 Order time V1.0 locked-in, updated gerbs
    [GeneralMCU-B_Cu.gbr, GeneralMCU-B_Mask.gbr, GeneralMCU-B_Paste.gbr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]
2019-10-18 Added indicator LED for braking
    [SolenoidSense.sch]
2019-10-18 Added inverter kill connectors.
    [Connectors.sch]
2019-10-18 Cleaned up comments. (sorry for the electrical alerts spam bys)
    [SolenoidSense.sch]
2019-10-22 Fixed current sense, added GP relay LEDs
    [Connectors.sch, Relays.sch, SolenoidAndPumpDrivers.sch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]
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2019-10-22 Updated Paraduino pinout (again)
    [Connectors.sch]
2019-10-25 Schematic lost in time, grab later from past commit. Added noncast version because we have no cashhhhhhhh
    [GeneralMCU - Old Layout.kicad_pcb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]
2019-10-28 Added caps on mounting holes, reversed connector polarity
    [Connectors.sch]
2019-10-28 XT30 sourcing and footprints
    [Connectors.sch]
2019-10-28 Switched to active low brake lines
    [Connectors.sch, SolenoidAndPumpDrivers.sch, SolenoidSense.sch]
2019-11-03 Generate netlist, started some very rough placement
    [SolenoidSense.sch]
2019-11-05 Initial layout pass. This will be changed many times I'm sure.
    [BigSur.kicad_pcb, Connectors.sch]
2019-11-05 Moved configuration passives for DRV103s.
    [BigSur.kicad_pcb]
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2019-11-11 Added custom 3d models for some parts, continued work on layout.
    [BigSur.kicad_pcb, BigSur.sch, Connectors.sch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]
2019-11-13 Made brake output active high in accordance with meeting decision
    [BigSur.kicad_pcb, BigSur.sch, Connectors.sch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]
2019-11-14 Moved connectors to fit new LV plate layout
    [BigSur.kicad_pcb]
2019-11-19 Squished output connectors together, going to need to fix layout.
    Also still needs CAN and inverter chill connectors.
    [BigSur.kicad_pcb, BigSur.sch, Connectors.sch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]
2019-11-21 Revert "Order time V1.0 locked-in, updated gerbs"
    This reverts commit a2b677ba43e52ec178062c1ac254df27289ef0f4.
    [GeneralMCU-B_Cu.gbr, GeneralMCU-B_Mask.gbr, GeneralMCU-B_Paste.gbr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]
2019-11-21 Used sch-bak to recover sch, updated pdf
    -bak sch seemed to be correct so I just used that instead of a past commit.
    [GeneralMCU.sch]
2019-11-21 Revert "Schematic lost in time, grab later from past commit. Added noncast version because we have no cashhhhhhhh"
    This reverts commit bf9f08a9f085a0130a5e5ccea324bcbd31a22aae.
    [GeneralMCU - Old Layout.kicad_pcb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]
2019-11-21 WE BACK BABY
    sorry for tying up master lol
    [GeneralMCU.sch]
2019-11-21 Adding in old rescued folder.
    [GeneralMCU - Old Layout.kicad_pcb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]
2019-11-25 Fixed braking LED direction
    [BigSur.kicad_pcb, BigSur.sch, Connectors.sch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]
2019-11-29 Finished another layout pass.
    [BigSur.kicad_pcb, Connectors.sch]
2020-05-25 Create general PCB MCU layout (Mojave)
    [PCB_Mojave.kicad_pcb, PCB_Mojave.sch]
2020-06-08 Merging back in to master
    [PCB_Mojave.sch]
2020-06-08 Update PCB_Mojave to use Hyperlib instead of project specific library
    [HyperlibTest.kicad_pcb, HyperlibTest.sch, PCB_Mojave.sch]
2020-07-16 Export STEP and dimension drawing, preparing to merge with master.
    [BigSur.kicad_pcb]
